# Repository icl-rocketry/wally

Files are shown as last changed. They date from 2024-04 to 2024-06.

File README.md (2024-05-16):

# Sirius

Sirius is a two stage rocket being designed and built by ICLR's Altitude Record Team (ART). This repository contains the avionics hardware and software for the rocket.

Sirius has multiple avionics systems on board, with a combination of COTS and SRAD boards used for maximum redundancy and functionality. 

COTS components used:
* [Featherweight Blue Raven](https://www.featherweightaltimeters.com/blue-raven-altimeter.html) flight computer (x2)
* [Featherweight GPS Tracker](https://www.featherweightaltimeters.com/featherweight-gps-tracker.html) (sustainer only)
* [Vodafone Curve](https://eshop.v.vodafone.com/uk/curve-gps-tracker) (booster only)

SRAD boards used:
* Pickle [(developed here)](https://github.com/icl-rocketry/Ricardo-PickleRick)
* WALLY
* Lockie
* PDU

This repository is used for the development of WALLY, Lockie, the PDU and various helper boards. 

## WALLY: Wide Area Landing Location sYstem

Wally complements the COTS trackers and the GPS system onboard Pickle to provide an independent method for trajectory reconstruction and telemetry.

It contains the following elements:
* Microcontroller - ESP32-S3
* GPS - SIM7600G
* LTE - SIM7600G
* RTC - DS3231
* 868MHz LoRa - SX1262
* Barometer - DSP368
* IMU
* Magnetometer
* Storage - Micro SD

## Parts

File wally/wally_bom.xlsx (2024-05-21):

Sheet: JLC
PCB Ident | Block | Description | Value | JLC Name | JLC Code | Basic | Cost | 0402 Code
C01 | Boost | Capacitor | 10u | CL10A106MA8NRNC | C96446 | Y | 0.0174 |  | JLC Subtotal | 0.5295
C02 | Boost | Capacitor | 10u | CL10A106MA8NRNC | C96446 | Y | 0.0174
C03 | Boost | Capacitor | 1u | CL10A105KB8NNNC | C15849 | Y | 0.0043 |  | Boards Total (USD, no VAT) | 46.13
C04 | Boost | Capacitor | 22u | CL10A226MQ8NRNC | C59461 | Y | 0.008 |  | Boards Total (GBP, VAT) | 44.2848
C05 | Boost | Capacitor | 22u | CL10A226MQ8NRNC | C59461 | Y | 0.008
C06 | Boost | Capacitor | 22u | CL10A226MQ8NRNC | C59461 | Y | 0.008 |  | Boards Ordered | 15
C07 | Boost | Capacitor | 22u | CL10A226MQ8NRNC | C59461 | Y | 0.008 |  | Unit Cost | 2.95232
C08 | Boost | Capacitor | 1u | CL10A105KB8NNNC | C15849 | Y | 0.0043
C09 | Boost | Capacitor | 100n | CC0603KRX7R9BB104 | C14663 | Y | 0.0021
C10 | LDO | Capacitor | 1u | CL10A105KB8NNNC | C15849 | Y | 0.0043
C11 | ESP | Capacitor | 100n | CC0603KRX7R9BB104 | C14663 | Y | 0.0021
C12 | ESP | Capacitor | 22u | CL10A226MQ8NRNC | C59461 | Y | 0.008
C13 | ESP | Capacitor | 100n | CC0603KRX7R9BB104 | C14663 | Y | 0.0021
C14 | USB | Capacitor | 100n | CC0603KRX7R9BB104 | C14663 | Y | 0.0021
C15 | USB | Capacitor | 1u | CL10A105KB8NNNC | C15849 | Y | 0.0043
C16 | ESP | Capacitor | 100n | CC0603KRX7R9BB104 | C14663 | Y | 0.0021
C17 | ESP | Capacitor | 100n | CC0603KRX7R9BB104 | C14663 | Y | 0.0021
C18 | ESP | Capacitor | 22u | CL10A226MQ8NRNC | C59461 | Y | 0.008
C19 | LORA | Capacitor | 100n | CC0603KRX7R9BB104 | C14663 | Y | 0.0021
C20 | Boost | Capacitor | 22u | CL10A226MQ8NRNC | C59461 | Y | 0.008
C21 | Boost | Capacitor | 22u | CL10A226MQ8NRNC | C59461 | Y | 0.008
C22 | Boost | Capacitor | 22u | CL10A226MQ8NRNC | C59461 | Y | 0.008
C23 | LORA | Capacitor | 10u | CL10A106KP8NNNC | C19702 | Y | 0.0055
C24 | IO | Capacitor | 470n | CL10B474KA8NNNC | C1623 | Y | 0.0069
C25 | IO | Capacitor | 470n | CL10B474KA8NNNC | C1623 | Y | 0.0069
C26 | IO | Capacitor | 100n | CC0603KRX7R9BB104 | C14663 | Y | 0.0021
C27 | IO | Capacitor | 100n | CC0603KRX7R9BB104 | C14663 | Y | 0.0021
C28 | IO | Capacitor | 100n | CC0603KRX7R9BB104 | C14663 | Y | 0.0021
C29 | IO | Capacitor | 100n | CC0603KRX7R9BB104 | C14663 | Y | 0.0021
C30 | Boost | Capacitor | 10u | CL10A106MA8NRNC | C96446 | Y | 0.0174
C31 | Boost | Capacitor | 10u | CL10A106MA8NRNC | C96446 | Y | 0.0174
C32 | Boost | Capacitor | 10u | CL10A106MA8NRNC | C96446 | Y | 0.0174
C33 | Boost | Capacitor | 10u | CL10A106MA8NRNC | C96446 | Y | 0.0174
C34 | Boost | Capacitor | 10u | CL10A106MA8NRNC | C96446 | Y | 0.0174
C35 | Boost | Capacitor | 100n | CC0603KRX7R9BB104 | C14663 | Y | 0.0021
C36 | Boost | Capacitor | 10u | CL10A106MA8NRNC | C96446 | Y | 0.0174
C39 | LDO | Capacitor | 22u | CL10A226MQ8NRNC | C59461 | Y | 0.008
C40 | LDO | Capacitor | 22u | CL10A226MQ8NRNC | C59461 | Y | 0.008
C41 | LDO | Capacitor | 22u | CL10A226MQ8NRNC | C59461 | Y | 0.008
C42 | LDO | Capacitor | 22u | CL10A226MQ8NRNC | C59461 | Y | 0.008
D1 | Boost | Schottky | SSA34-E3 | SS54 | C22452 | Y | 0.0422
D2 | USB | Schottky | SSA34-E3 | SS54 | C22452 | Y | 0.0422
L1 | Boost | Inductor | 10uH | SDFL1608S100KTF | C1035 | Y | 0.0097
LED1 | IO | LED | LEDG | KT-0805G | C2297 | y | 0.0132
LED2 | USB | LED | LEDW | KT-0805W | C34499 | Y | 0.0156
LED3 | USB | LED | LEDY | KT-0805Y | C2296 | Y | 0.0118
R01 | ESP | Resistor | 10k | 0603WAF1002T5E | C25804 | Y | 0.0009
R02 | Boost | Resistor | 1M | 0603WAF1004T5E | C22935 | Y | 0.0009
R03 | Boost | Resistor | 120k | 0603WAF1203T5E | C25808 | Y | 0.0009
R04 | ESP | Resistor | 1k | 0603WAF1001T5E | C21190 | Y | 0.0009
R05 | IO | Resistor | 10k | 0603WAF1002T5E | C25804 | Y | 0.0009
R06 | IO | Resistor | 10k | 0603WAF1002T5E | C25804 | Y | 0.0009
R07 | IO | Resistor | 10k | 0603WAF1002T5E | C25804 | Y | 0.0009
R08 | IO | Resistor | 10k | 0603WAF1002T5E | C25804 | Y | 0.0009
R09 | ESP | Resistor | 100k | 0603WAF1003T5E | C25803 | Y | 0.0009
R10 | ESP | Resistor | 20k | 0603WAF2002T5E | C4184 | Y | 0.0009
R11 | ESP | Resistor | 1k | 0603WAF1001T5E | C21190 | Y | 0.0009
R12 | USB | Resistor | 5k1 | 0603WAF5101T5E | C23186 | Y | 0.0009
R13 | USB | Resistor | 1M | 0603WAF1004T5E | C22935 | Y | 0.0009
R14 | USB | Resistor | 5k1 | 0603WAF5101T5E | C23186 | Y | 0.0009
R15 | IO | Resistor | 33 | 0603WAF330JT5E | C23140 | Y | 0.0009
R16 | ESP | Resistor | 100 | 0603WAF1000T5E | C22775 | Y | 0.001
R17 | IO | Resistor | 150 | 0603WAF1500T5E | C22808 | Y | 0.0009
LED4 | IO | LED | LEDG | KT-0805G | C2297 | y | 0.0132
LED5 | IO | LED | LEDG | KT-0805G | C2297 | y | 0.0132
LED6 | IO | LED | LEDR | NCD0805R1 | C84256 | y | 0.0126
R18 | IO | Resistor | 33 | 0603WAF330JT5E | C23140 | Y | 0.0009
R19 | IO | Resistor | 33 | 0603WAF330JT5E | C23140 | Y | 0.0009
R20 | IO | Resistor | 51 | 0603WAF510JT5E | C23197 | Y | 0.0009
S1 | IO | Switch |  | TS-1187A-B-A-B | C318884 | Y | 0.0164
S2 | IO | Switch |  | TS-1187A-B-A-B | C318884 | Y | 0.0164

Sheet: Flight Version
PCB Ident | Desc | Name | Link | Supplier | Unit Cost | Quantity Required | Subtotal | Optional | added to order
U1 | LoRa Module | AI Thinker RA-01SH | https://www.aliexpress.com/item/1005002561194884.html | Aliexpress | 3.535555556 | 1 | 3.535555556 | n | y | Mandatory Components | 21.22555556
IC1 | MCU | ESP32-S3-WROOM-1-N16R2 | https://www.mouser.co.uk/ProductDetail/Espressif-Systems/ESP32-S3-WROOM-1-N16R2 | Mouser | 2.9 | 1 | 2.9 | n | y | Optional Components | 40.95
IC2 | Boost | TI TLV61048DBVR | https://www.mouser.co.uk/ProductDetail/Texas-Instruments/TLV61048DBVR?qs=vLWxofP3U2yo%2F8t1L3OASw%3D%3D | Mouser | 0.56 | 1 | 0.56 | n | y | Board manufacture cost | 2.95232
IC3 | LDO | TLV1117LV33DCYR | https://www.mouser.co.uk/ProductDetail/Texas-Instruments/TLV1117LV33DCYR?qs=tEz3BkPb1rwzXMb8FiWhow%3D%3D | Mouser | 0.28 | 1 | 0.28 | n | y
J1 | Micro SD | MSD-4-A | https://www.mouser.co.uk/ProductDetail/CUI-Devices/MSD-4-A?qs=Z%252BL2brAPG1Jll%252BQTi%252Btupg%3D%3D | Mouser | 0.28 | 1 | 0.28 | n | y | Per Board Total | 65.12787556
USB | USB C Port | USB4105-GF-A-120 | https://www.mouser.co.uk/ProductDetail/GCT/USB4105-GF-A-120?qs=QNEnbhJQKva%252Bjxw%2FpEjDhQ%3D%3D | Mouser | 0.66 | 1 | 0.66 | n | y | Boards Required | 1
SIM | LTE Module | SIM 7600G | https://www.aliexpress.com/item/4000449295553.html | Aliexpress | 29.33 | 1 | 29.33 | y | y
IC4 | Barometer | DPS368XTSA1 | https://www.mouser.co.uk/ProductDetail/Infineon-Technologies/DPS368XTSA1?qs=l7cgNqFNU1issZx9oeCNag%3D%3D | Mouser | 2.49 | 1 | 2.49 | n | y | Total | 65.12787556
IC9 | Env sensor | BME680 | https://www.mouser.co.uk/ProductDetail/Bosch-Sensortec/BME680?qs=v271MhAjFHjo0yA%2FC4OnDQ%3D%3D | Mouser | 8.61 | 1 |  | y | y
IC8 | Light sensor | APSD-9523 | https://www.mouser.co.uk/ProductDetail/Broadcom-Avago/APDS-9253-001?qs=T3oQrply3y9os9rwnJ1p%252Bg%3D%3D | Mouser | 1.97 | 2 |  | y | y
IC7 | Mag | MMC5983 | https://www.mouser.co.uk/ProductDetail/MEMSIC/MMC5983MA?qs=B6kkDfuK7%2FD5qasHMdEt2g%3D%3D | Mouser | 2.88 | 2 |  | n | y
RTC | RTC | DS3231 | https://www.aliexpress.com/item/1005006254225186.html | Aliexpress | 0.87 | 1 | 0.87 | y | y
IC6 | IMU | LSM6DSV32 | https://www.mouser.co.uk/ProductDetail/STMicroelectronics/LSM6DSV32XTR?qs=HoCaDK9Nz5d%252BGVBpjxkjlg%3D%3D | Mouser | 5.26 | 2 | 10.52 | n | y
AC1 | Accelerometer | H3LIS331 | https://www.mouser.co.uk/ProductDetail/STMicroelectronics/H3LIS331DLTR?qs=TAo1I7FhABsAZFqkqNUSRA%3D%3D | Mouser | 10.75 | 1 | 10.75 | y | y

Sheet: Ground Version
PCB Ident | Desc | Name | Link | Supplier | Unit Cost | Quantity Required | Subtotal | Optional
U1 | LoRa Module | AI Thinker RA-01SH | https://www.aliexpress.com/item/1005002561194884.html | Aliexpress | 3.535555556 | 1 | 3.535555556 | n | Mandatory Components | 10.12555556
IC1 | MCU | ESP32-S3-WROOM-1-N16R2 | https://www.mouser.co.uk/ProductDetail/Espressif-Systems/ESP32-S3-WROOM-1-N16R2 | Mouser | 2.9 | 1 | 2.9 | n | Optional Components | 0.87
IC2 | Boost | TI TLV61048DBVR | https://www.mouser.co.uk/ProductDetail/Texas-Instruments/TLV61048DBVR?qs=vLWxofP3U2yo%2F8t1L3OASw%3D%3D | Mouser | 0.56 | 1 | 0.56 | n | Board manufacture cost | 2.95232
IC3 | LDO | TLV1117LV33DCYR | https://www.mouser.co.uk/ProductDetail/Texas-Instruments/TLV1117LV33DCYR?qs=tEz3BkPb1rwzXMb8FiWhow%3D%3D | Mouser | 0.28 | 1 | 0.28 | n
J1 | Micro SD | MSD-4-A | https://www.mouser.co.uk/ProductDetail/CUI-Devices/MSD-4-A?qs=Z%252BL2brAPG1Jll%252BQTi%252Btupg%3D%3D | Mouser | 0.28 | 1 | 0.28 | n | Per Board Total | 13.94787556
USB | USB C Port | 217175-0001 | https://www.mouser.co.uk/ProductDetail/Molex/217175-0001?qs=DRkmTr78QARWJMiqNnldSg%3D%3D | Mouser | 0.65 | 1 | 0.65 | n | Boards Required | 6
GPS | GPS Module | NEO-7M | https://www.aliexpress.com/item/1005005475472834.html | Aliexpress | 1.92 | 1 | 1.92 | n
RTC | RTC | DS3231 | https://www.aliexpress.com/item/1005006254225186.html | Aliexpress | 0.87 | 1 | 0.87 | y | Total | 101.4011733

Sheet: JLC_Extended
PCB Ident | Block | Description | Value | JLC Name | JLC Code | Unit Cost | Total Cost
J5 | USB | USB C Connector |  | MC-107DB | C3039324 | 0.1683 | 5.5245 | Part Subtotal | 91.119
IC2 | Power | Boost converter |  | TLV61048DBVR | C2861467 | 0.204 | 6.06
IC5 | Sensors | IMU |  | BMI323 | C5368700 | 1.4025 | 24.0375
IC4 | Sensors | Baro |  | DPS368 | C3232508 | 3.1455 | 50.1825
IC3 | Power | LDO |  | TLV1117LV33DCYR | C15578 | 0.1543 | 5.3145
 |  |  |  |  |  |  |  | Boards Ordered | 15
 |  |  |  |  |  |  |  | Unit Cost | 6.0746

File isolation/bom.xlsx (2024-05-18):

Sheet: JLC
PCB Ident | Block | Description | Simple Name | JLC Name | JLC Code | Basic | Cost
D1 | Power | Schottky | Schottky Diode 5A | SS54 | C22452 | Y | 0.0422 | JLC Subtotal | 0.4518
C02 | Power | Boost end cap | 20V 10u cap | CL10A106MA8NRNC | C96446 | Y | 0.0174
C16 | Output | Bulk Cap | 20V 10u cap | CL10A106MA8NRNC | C96446 | Y | 0.0174 | Boards Total (USD, no VAT) | 37.27
C17 | Output | Bulk Cap | 20V 10u cap | CL10A106MA8NRNC | C96446 | Y | 0.0174 | Boards Total (GBP, VAT) | 35.7792
C18 | Output | Bulk Cap | 20V 10u cap | CL10A106MA8NRNC | C96446 | Y | 0.0174
C19 | Output | Bulk Cap | 20V 10u cap | CL10A106MA8NRNC | C96446 | Y | 0.0174 | Boards Ordered | 10
LED01 | Battery | Pow LED | White LED | KT-0805W | C34499 | Y | 0.0156 | Unit Cost | 3.57792
LED03 | Lock | Disabled LED | Green LED | KT-0805G | C2297 | y | 0.0132
LED05 | Lock | Disabled LED | Green LED | KT-0805G | C2297 | y | 0.0132
LED06 | Indicator | Show firing channel | Red LED | NCD0805R1 | C84256 | Y | 0.0126
LED07 | Indicator | Show firing channel | Red LED | NCD0805R1 | C84256 | Y | 0.0126
LED08 | Indicator | Show firing channel | Red LED | NCD0805R1 | C84256 | Y | 0.0126
LED09 | Indicator | Show firing channel | Red LED | NCD0805R1 | C84256 | Y | 0.0126
LED10 | Indicator | Show firing channel | Red LED | NCD0805R1 | C84256 | Y | 0.0126
LED11 | Indicator | Show firing channel | Red LED | NCD0805R1 | C84256 | Y | 0.0126
LED12 | Indicator | Show firing channel | Red LED | NCD0805R1 | C84256 | Y | 0.0126
LED13 | Indicator | Show firing channel | Red LED | NCD0805R1 | C84256 | Y | 0.0126
LED14 | Indicator | Show firing channel | Red LED | NCD0805R1 | C84256 | Y | 0.0126
LED02 | Lock | Enable LED | Yellow LED | KT-0805Y | C2296 | Y | 0.0118
LED04 | Lock | Enable LED | Yellow LED | KT-0805Y | C2296 | Y | 0.0118
L1 | Power | Inductor | 10uH inductor | SDFL1608S100KTF | C1035 | Y | 0.0097
C04 | Power | Input Cap | 22u cap | CL10A226MQ8NRNC | C59461 | Y | 0.008
C05 | Power | Input Cap | 22u cap | CL10A226MQ8NRNC | C59461 | Y | 0.008
C06 | Power | Input Cap | 22u cap | CL10A226MQ8NRNC | C59461 | Y | 0.008
C07 | Power | Input Cap | 22u cap | CL10A226MQ8NRNC | C59461 | Y | 0.008
C20 | Power | Bulk Cap | 22u cap | CL10A226MQ8NRNC | C59461 | Y | 0.008
C21 | Power | Bulk Cap | 22u cap | CL10A226MQ8NRNC | C59461 | Y | 0.008
C22 | Power | Bulk Cap | 22u cap | CL10A226MQ8NRNC | C59461 | Y | 0.008
D2 | USB | Drop Diode | Diode | SM4007PL | C64898 | Y | 0.0068
D3 | USB | Drop Diode | Diode | SM4007PL | C64898 | Y | 0.0068
D4 | USB | Drop Diode | Diode | SM4007PL | C64898 | Y | 0.0068
C01 | Power | Input Cap | 10V 10u cap | CL10A106KP8NNNC | C19702 | Y | 0.0055
C03 | Power | Rectifier Cap | 1u cap | CL10A105KB8NNNC | C15849 | Y | 0.0043
C09 | Logic | Inverter Cap | 1u cap | CL10A105KB8NNNC | C15849 | Y | 0.0043
C11 | Logic | Inverter Cap | 1u cap | CL10A105KB8NNNC | C15849 | Y | 0.0043
C13 | Logic | Inverter Cap | 1u cap | CL10A105KB8NNNC | C15849 | Y | 0.0043
C15 | USB | Filter Cap | 1u cap | CL10A105KB8NNNC | C15849 | Y | 0.0043
C08 | Logic | Inverter Cap | 100n cap | CC0603KRX7R9BB104 | C14663 | Y | 0.0021
C10 | Logic | Inverter Cap | 100n cap | CC0603KRX7R9BB104 | C14663 | Y | 0.0021
C12 | Logic | Inverter Cap | 100n cap | CC0603KRX7R9BB104 | C14663 | Y | 0.0021
C14 | USB | Filter Cap | 100n cap | CC0603KRX7R9BB104 | C14663 | Y | 0.0021
R01 | Battery | Pow LED R | R 75 | 0603WAF750JT5E | C4275 | Y | 0.001
R04 | Lock | Enable LED R | R 120 | 0603WAF1200T5E | C22787 | Y | 0.001
R05 | Lock | Enable LED R | R 120 | 0603WAF1200T5E | C22787 | Y | 0.001
R06 | Lock | Disabled LED R | R 100 | 0603WAF1000T5E | C22775 | Y | 0.001
R07 | Lock | Disabled LED R | R 100 | 0603WAF1000T5E | C22775 | Y | 0.001
R15 | Indicator | LED R | R 120 | 0603WAF1200T5E | C22787 | Y | 0.001
R16 | Indicator | LED R | R 120 | 0603WAF1200T5E | C22787 | Y | 0.001
R17 | Indicator | LED R | R 120 | 0603WAF1200T5E | C22787 | Y | 0.001
R18 | Indicator | LED R | R 120 | 0603WAF1200T5E | C22787 | Y | 0.001
R19 | Indicator | LED R | R 120 | 0603WAF1200T5E | C22787 | Y | 0.001
R20 | Indicator | LED R | R 120 | 0603WAF1200T5E | C22787 | Y | 0.001
R21 | Indicator | LED R | R 120 | 0603WAF1200T5E | C22787 | Y | 0.001
R22 | Indicator | LED R | R 120 | 0603WAF1200T5E | C22787 | Y | 0.001
R23 | Indicator | LED R | R 120 | 0603WAF1200T5E | C22787 | Y | 0.001
R02 | Power | V Div R1 | R 1M | 0603WAF1004T5E | C22935 | Y | 0.0009
R03 | Power | V Div R2 | R 68k | 0603WAF6802T5E | C23231 | Y | 0.0009
R08 | Relay | Pulldown R | R 68k | 0603WAF6802T5E | C23231 | Y | 0.0009
R09 | Relay | Pulldown R | R 68k | 0603WAF6802T5E | C23231 | Y | 0.0009
R10 | Relay | Pulldown R | R 68k | 0603WAF6802T5E | C23231 | Y | 0.0009
R11 | Relay | Pulldown R | R 68k | 0603WAF6802T5E | C23231 | Y | 0.0009
R12 | USB | Pulldown R | R 5k1 | 0603WAF5101T5E | C23186 | Y | 0.0009
R13 | USB | Protection R | R 1M | 0603WAF1004T5E | C22935 | Y | 0.0009
R14 | USB | Pulldown R | R 5k1 | 0603WAF5101T5E | C23186 | Y | 0.0009

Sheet: Other
PCB Ident | Desc | Name | Link | Supplier | Unit Cost | Added to order
 | Buzzer | CMI-9705-85-SMT-TR | https://www.mouser.co.uk/ProductDetail/CUI-Devices/CMI-9705-85-SMT-TR?qs=P1JMDcb91o4Wun0lW9vptg%3D%3D | Mouser | 1.2 | y | Components Total | 6.346
E1 | Input | SJ1-3525N | https://www.mouser.co.uk/ProductDetail/CUI-Devices/SJ1-3525N?qs=WyjlAZoYn505QPmBO3I74g%3D%3D | Mouser | 0.88 | y | Boards Cost | 3.57792
E2 | Input | SJ1-3525N | https://www.mouser.co.uk/ProductDetail/CUI-Devices/SJ1-3525N?qs=WyjlAZoYn505QPmBO3I74g%3D%3D | Mouser | 0.88 | y
USB | USB C Port | UJC-HP2-3-SMT-TR | https://www.mouser.co.uk/ProductDetail/CUI-Devices/UJC-HP2-3-SMT-TR?qs=HoCaDK9Nz5cglCCyoWNzZg%3D%3D | Mouser | 0.464 | y
IC1 | Boost | TI TLV61048DBVR | https://www.mouser.co.uk/ProductDetail/Texas-Instruments/TLV61048DBVR?qs=vLWxofP3U2yo%2F8t1L3OASw%3D%3D | Mouser | 0.552 | y | Board Subtotal | 9.92392
IC5 | MOSFET | FDN359BN | https://www.mouser.co.uk/ProductDetail/onsemi-Fairchild/FDN359BN?qs=8YYpzd7qSxKZfze3Gm99uA%3D%3D | Mouser | 0.37 | y | Boards Required | 6
IC6 | MOSFET | FDN359BN | https://www.mouser.co.uk/ProductDetail/onsemi-Fairchild/FDN359BN?qs=8YYpzd7qSxKZfze3Gm99uA%3D%3D | Mouser | 0.37 | y | Total Cost | 59.54352
IC7 | MOSFET | FDN359BN | https://www.mouser.co.uk/ProductDetail/onsemi-Fairchild/FDN359BN?qs=8YYpzd7qSxKZfze3Gm99uA%3D%3D | Mouser | 0.37 | y
IC8 | MOSFET | FDN359BN | https://www.mouser.co.uk/ProductDetail/onsemi-Fairchild/FDN359BN?qs=8YYpzd7qSxKZfze3Gm99uA%3D%3D | Mouser | 0.37 | y
IC3 | OR gate | SN74HCS32BQAR | https://www.mouser.co.uk/ProductDetail/Texas-Instruments/SN74HCS32BQAR?qs=stqOd1AaK78oD0q8sZ5E5Q%3D%3D | Mouser | 0.32 | y
IC2 | Inverter | SN74HC14PWR | https://www.mouser.co.uk/ProductDetail/Texas-Instruments/SN74HC14PWR?qs=YEaxc5757jODQ8PDizZzPA%3D%3D | Mouser | 0.31 | y
IC4 | AND gate | SN74HCS08DYYR | https://www.mouser.co.uk/ProductDetail/Texas-Instruments/SN74HCS08DYYR?qs=Li%252BoUPsLEnuxOc6m1Nu7zQ%3D%3D | Mouser | 0.26 | y
J1 | Input | JST-PH 4 pin
J2 | Input | JST-PH 4 pin
J3 | Output | JST-PH 2 pin
J4 | Output | JST-PH 2 pin
J5 | Output | JST-PH 2 pin
BAT1 | Power | JST-PH 2 pin
BAT2 | Power | JST-PH 2 pin

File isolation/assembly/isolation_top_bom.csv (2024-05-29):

Comment | Designator | Footprint | LCSC Part #
1M | R2 R13 | RESC1005X40 | C26083
1u | C3 C9 C11 C13 C15 C25 | CAPC1005X60 | C52923
5k1 | R12 R14 | RESC1005X40 | C25905
10u | C1 | CAPC1005X60 | C15525
10u | C2 C16 C17 C18 C19 C23 | CAPC1608X85 | C96446
10μH | L1 | BMRF00060630100MA1 | C305184
22u | C4 C5 C6 C7 C20 C21 C22 | CAPC1608X85 | C59461
47k | R6 R7 R8 R9 R10 R11 R28 R29 R30 R31 | RESC1005X40 | C25792
68k | R3 | RESC1608X60 | C23231
75 | R1 | RESC1608X60 | C4275
100n | C8 C10 C12 C14 C24 | CAPC1005X60 | C1525
120 | R4 R5 R15 R16 R17 R18 R19 R20 R21 R22 R23 | RESC1005X40 | C25079
470 | R24 R25 R26 R27 | RESC1005X40 | C25117
10164359-00011LF | J7 | 1016435900011LF
CMI-9705-85-SMT-TR | LS1 | CMI970585SMTTR
FDN359BN | IC5 IC6 IC7 IC8 | SOT95P251X112-3N | C5290365
LEDR | LED6 LED7 LED8 LED9 LED10 LED11 LED12 LED13 LED14 | CHIPLED_0805 | C84256
LEDW | LED1 | CHIPLED_0805 | C34499
LEDY | LED2 LED4 | CHIPLED_0805 | C2296
SN74HC14PWR | IC2 IC9 | SOP65P640X120-14N | C6821
SN74HCS08BQAR | IC4 | SN74HCS08BQAR | C4470281
SN74HCS32BQAR | IC3 | SN74HCS32BQAR | C4471379
SSA34-E3_5AT | D1 | DIOM5127X229N | C22452
USBDiode | D2 | SOD-123FL | C64898
XTLV61048DBVR | IC1 | SOT95P280X145-6N | C2861467

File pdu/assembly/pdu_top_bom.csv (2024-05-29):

Comment | Designator | Footprint | LCSC Part #
1u | C5 C8 C11 C14 C17 C20 C23 C26 C29 C32 | CAPC1608X85 | C15849
22u | C6 C9 C12 C15 C18 C21 C24 C27 C30 C33 | CAPC1608X85 | C59461
68k | R2 | RESC1608X60 | C23231
100 | R6 | RESC1608X60 | C22775
100n | C4 C7 C10 C13 C16 C19 C22 C25 C28 C31 | CAPC1608X85 | C14663
120 | R4 | RESC1608X60 | C22787
470 | R1 | RESC1608X60 | C23179
LEDG | LED3 | CHIPLED_0805 | C2297
LEDY | LED2 | CHIPLED_0805 | C2296
TSM4806CS_RLG | Q1 | SOP127P600X200-8N

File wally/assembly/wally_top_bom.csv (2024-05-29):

Comment | Designator | Footprint | LCSC Part #
1M | R2 | RESC1608X60 | C22935
1M | R13 | RESC1005X40 | C26083
1k | R4 R11 | RESC1005X40 | C11702
1u | C3 C8 C10 C15 C44 C46 | CAPC1005X60 | C52923
5k1 | R5 R6 R7 R8 | RESC1005X40 | C25905
5k1 | R12 R14 | RESC1608X60 | C23186
10k | R1 | RESC1005X40 | C25744
10u | C1 | CAPC1005X60 | C15525
10u | C2 | CAPC1608X85 | C96446
10u | C23 C24 | CAPC1005X60 | C15525
10u | C30 C31 C32 C33 C34 C36 | CAPC1608X85 | C96446
10uH | L1 | BMRF00060630100MA1
20k | R10 | RESC1005X40 | C25765
22u | C4 C5 C6 C7 C12 C18 C20 C21 C22 C39 C40 C41 C42 | CAPC1608X85 | C59461
33 | R15 R18 | RESC1005X40 | C25105
51 | R20 | RESC1608X60 | C23197
75 | R19 | RESC1608X60 | C4275
100 | R16 | RESC1005X40 | C25076
100k | R9 | RESC1005X40 | C25741
100n | C9 C11 C13 C14 C16 C17 C19 C25 C26 C27 C28 C29 C35 C37 C38 C43 C45 | CAPC1005X60 | C1525
120k | R3 | RESC1608X60 | C25808
150 | R17 | RESC1608X60 | C22808
APDS-9253-001 | IC8 | APDS9253001
BME688 | IC9 | BME688
DPS368XTSA1 | IC4 | DPS368XTSA1
ESP32-S3-WROOM-1U-N16 | IC1 | ESP32S3WROOM1UN16
H3LIS331DLTR | AC1 | LIS3DHTR
JUMPER-SMT_2_NO_SILK | JP4 JP5 | SMT-JUMPER_2_NO_SILK
LEDG | LED1 LED4 | CHIPLED_0805 | C2297
LEDR | LED6 | CHIPLED_0805 | C84256
LEDW | LED2 | CHIPLED_0805 | C34499
LEDY | LED3 LED5 | CHIPLED_0805 | C2296
LSM6DSV16BXTR | IC6 | LSM6DSV16BXTR
MMC5983MA | IC7 | MMC5983MA
MSD-4-A | J1 | MSD4A
QWIIC_RIGHT_ANGLE | J2 J3 | JST04_1MM_RA
RA-01H | U1 | XCVR_RA-01H
SSA34-E3_5AT | D1 D2 | DIOM5127X229N | C22452
TLV1117LV33DCYR | IC3 | SOT230P700X180-4N | C15578
TS-1187A-B-A-B | S1 S2 | TS1187ABAB | C318884
USB4105-GF-A | J5 | GCT_USB4105-GF-A | C3039324
XTLV61048DBVR | IC2 | SOT95P280X145-6N | C2861467

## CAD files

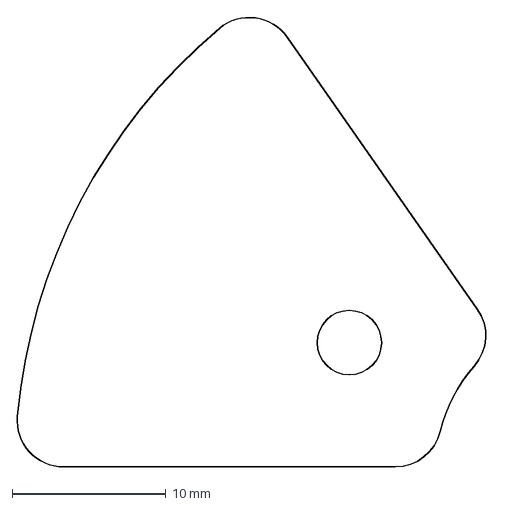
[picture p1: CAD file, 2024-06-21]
helpers/sustainer_ps.dxf
30.8 x 29.3 mm

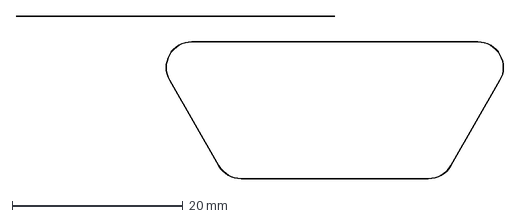
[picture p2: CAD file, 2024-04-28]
isolation/cutout.dxf
57.1 x 19.0 mm

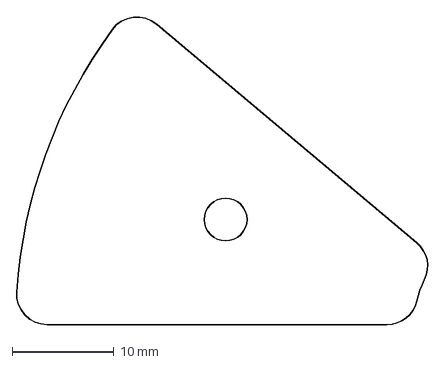
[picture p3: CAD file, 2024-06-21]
helpers/booster_ps.dxf
40.7 x 30.3 mm

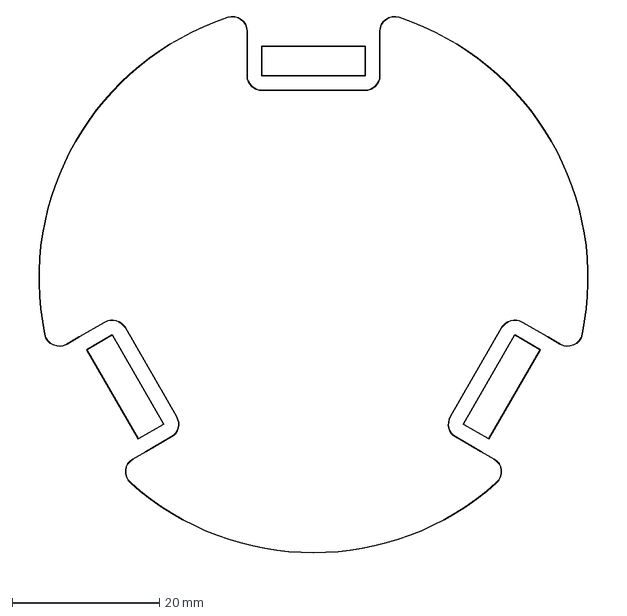
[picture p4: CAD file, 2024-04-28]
isolation/outline.dxf
80.7 x 76.0 mm

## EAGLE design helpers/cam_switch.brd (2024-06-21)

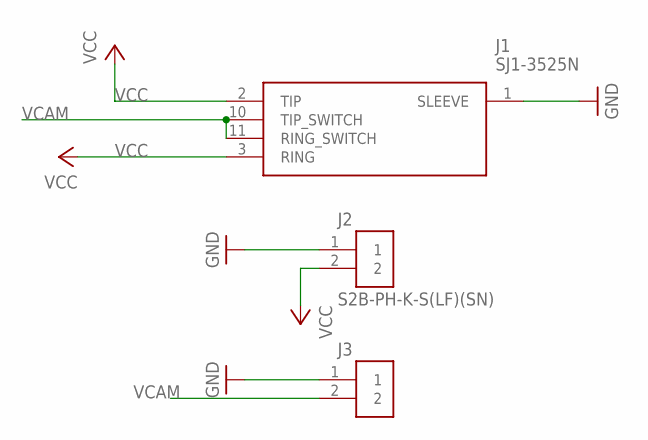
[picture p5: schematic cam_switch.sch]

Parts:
J1: SJ1-3525N; SJ13525N
J2, J3: S2B-PH-K-S(LF)(SN)

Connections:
GND: J1.1 (SLEEVE), J2.1, J3.1
VCAM: J1.10 (TIP_SWITCH), J1.11 (RING_SWITCH), J3.2
VCC: J1.2 (TIP), J1.3 (RING), J2.2

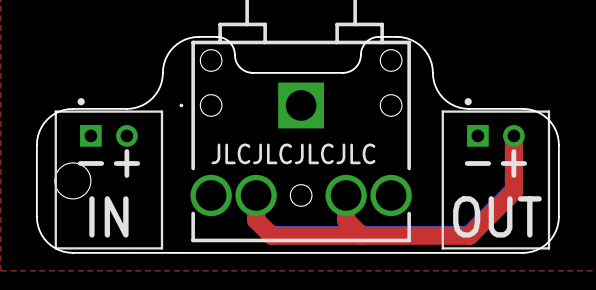
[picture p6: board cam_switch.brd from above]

Board: 2 copper layers, 29.0 x 12.0 mm, 3 parts (0 on the bottom side), 3 nets.

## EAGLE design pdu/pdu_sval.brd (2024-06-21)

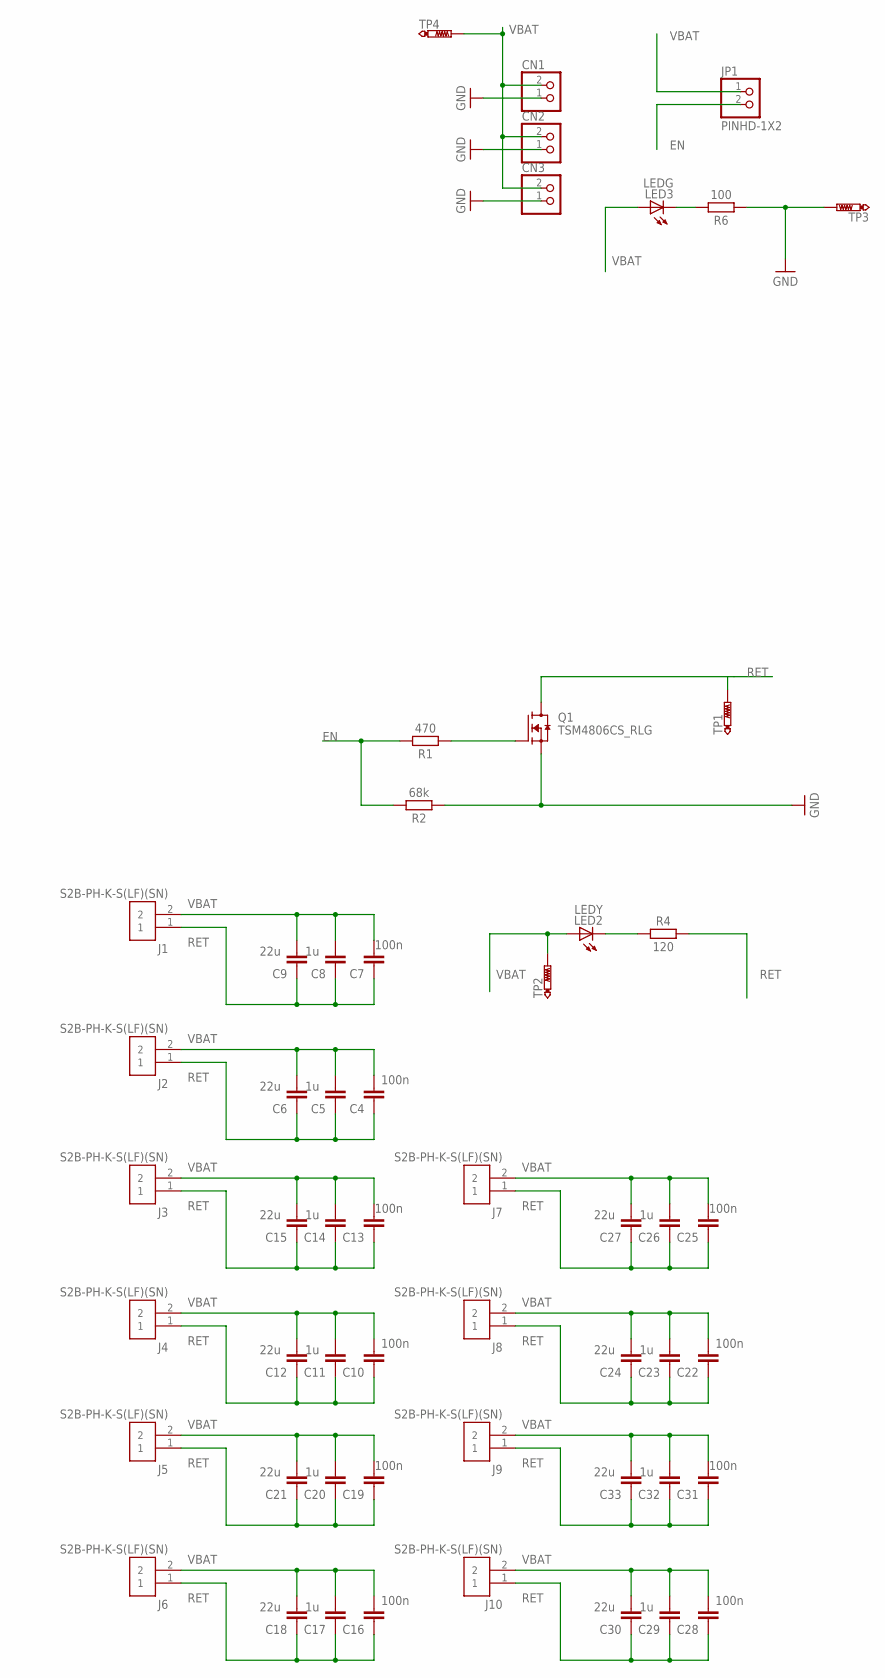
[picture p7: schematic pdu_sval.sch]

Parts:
C4, C7, C10, C13, C16, C19, C22, C25, C28, C31: 100n; CAPC1608X85
C5, C8, C11, C14, C17, C20, C23, C26, C29, C32: 1u; CAPC1608X85
C6, C9, C12, C15, C18, C21, C24, C27, C30, C33: 22u; CAPC1608X85
CN1, CN2, CN3: JST_2PIN-THM-RA; JST-PH-2-THM-RA
J1, J2, J3, J4, J5, J6, J7, J8, J9, J10: S2B-PH-K-S(LF)(SN)
JP1: PINHD-1X2; 1X02
LED2: LEDY; CHIPLED_0805
LED3: LEDG; CHIPLED_0805
Q1: TSM4806CS_RLG; SOP127P600X200-8N
R1: 470; RESC1608X60
R2: 68k; RESC1608X60
R4: 120; RESC1608X60
R6: 100; RESC1608X60
TP1, TP2, TP3, TP4: PTR1PAD1-13; P1-13

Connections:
EN: JP1.2, R1.2, R2.2
GND: CN1.1 (2), CN2.1 (2), CN3.1 (2), Q1.1 (S), Q1.2 (S), Q1.3 (S), R2.1, R6.1, TP3.TP
unnamed: Q1.4 (G), R1.1
unnamed: LED3.C, R6.2
unnamed: LED2.C, R4.1
RET: C4.1, C5.1, C6.1, C7.1, C8.1, C9.1, C10.1, C11.1, C12.1, C13.1, C14.1, C15.1, C16.1, C17.1, C18.1, C19.1, C20.1, C21.1, C22.1, C23.1, C24.1, C25.1, C26.1, C27.1, C28.1, C29.1, C30.1, C31.1, C32.1, C33.1, J1.1, J2.1, J3.1, J4.1, J5.1, J6.1, J7.1, J8.1, J9.1, J10.1, Q1.5 (D), Q1.6 (D), Q1.7 (D), Q1.8 (D), R4.2, TP1.TP
VBAT: C4.2, C5.2, C6.2, C7.2, C8.2, C9.2, C10.2, C11.2, C12.2, C13.2, C14.2, C15.2, C16.2, C17.2, C18.2, C19.2, C20.2, C21.2, C22.2, C23.2, C24.2, C25.2, C26.2, C27.2, C28.2, C29.2, C30.2, C31.2, C32.2, C33.2, CN1.2 (1), CN2.2 (1), CN3.2 (1), J1.2, J2.2, J3.2, J4.2, J5.2, J6.2, J7.2, J8.2, J9.2, J10.2, JP1.1, LED2.A, LED3.A, TP2.TP, TP4.TP

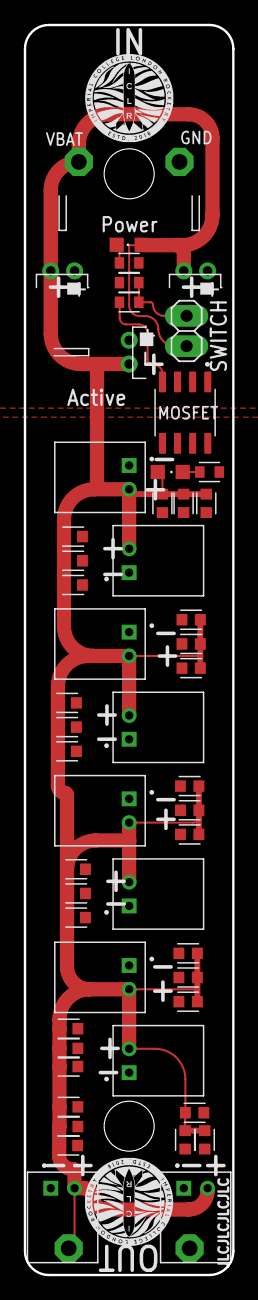
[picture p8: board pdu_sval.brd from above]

Board: 2 copper layers, 17.5 x 105.0 mm, 55 parts (0 on the bottom side), 7 nets.

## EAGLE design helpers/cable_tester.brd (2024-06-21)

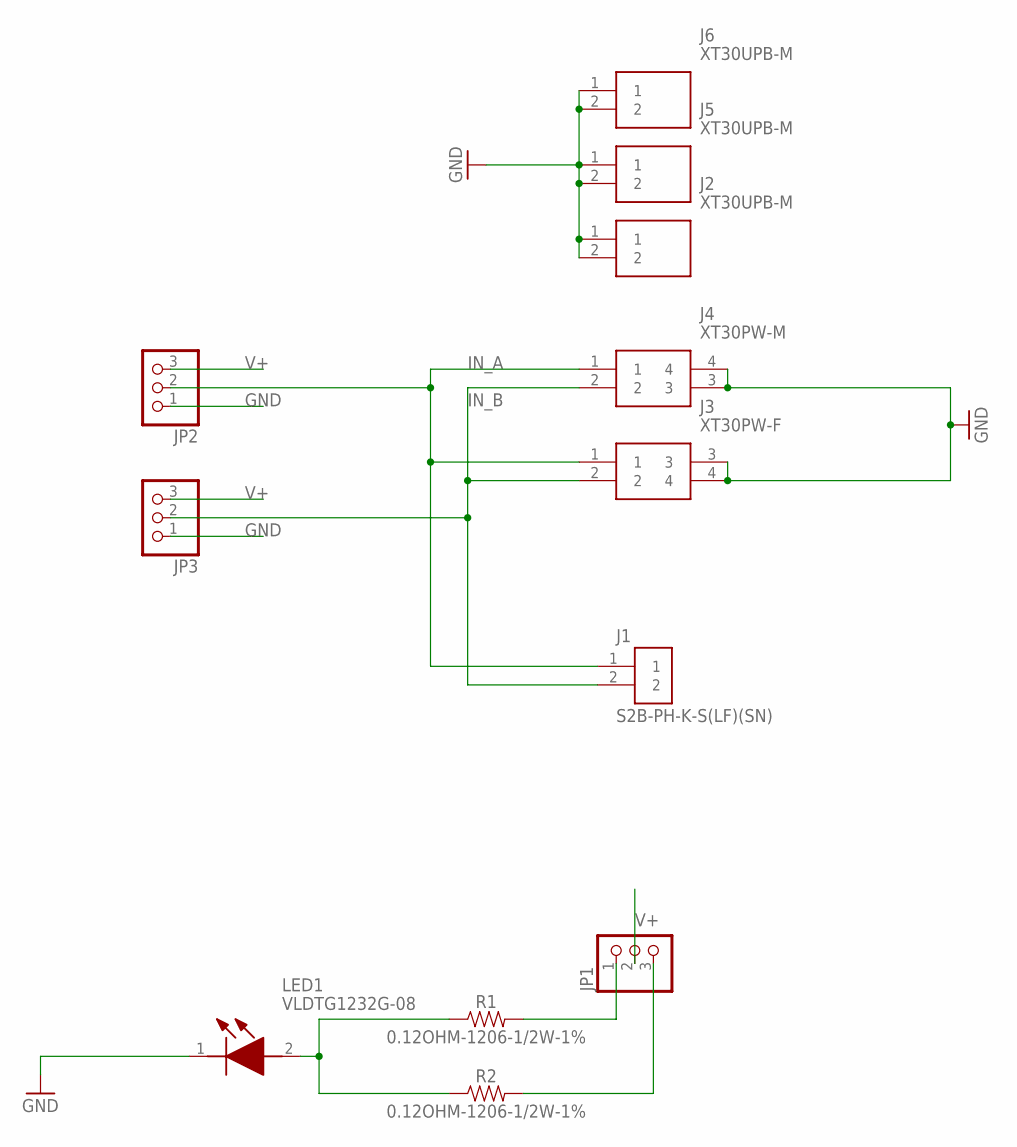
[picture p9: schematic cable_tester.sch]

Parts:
J1: S2B-PH-K-S(LF)(SN)
J2, J5, J6: XT30UPB-M; SHDR2W160P0X500_1X2_1020X520X1
J3: XT30PW-F; XT30PWF
J4: XT30PW-M; XT30PWM
JP1, JP2, JP3: PINHD-1X3; 1X03
LED1: VLDTG1232G-08; VLDTG1232G08
R1, R2: 0.12OHM-1206-1/2W-1%; 1206

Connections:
GND: J2.1, J2.2, J3.3, J3.4, J4.3, J4.4, J5.1, J5.2, J6.1, J6.2, JP2.1, JP3.1, LED1.1 (K)
IN_A: J1.1, J3.1, J4.1, JP2.2
IN_B: J1.2, J3.2, J4.2, JP3.2
unnamed: LED1.2 (A), R1.1, R2.1
unnamed: JP1.1, R1.2
unnamed: JP1.3, R2.2
V+: JP1.2, JP2.3, JP3.3

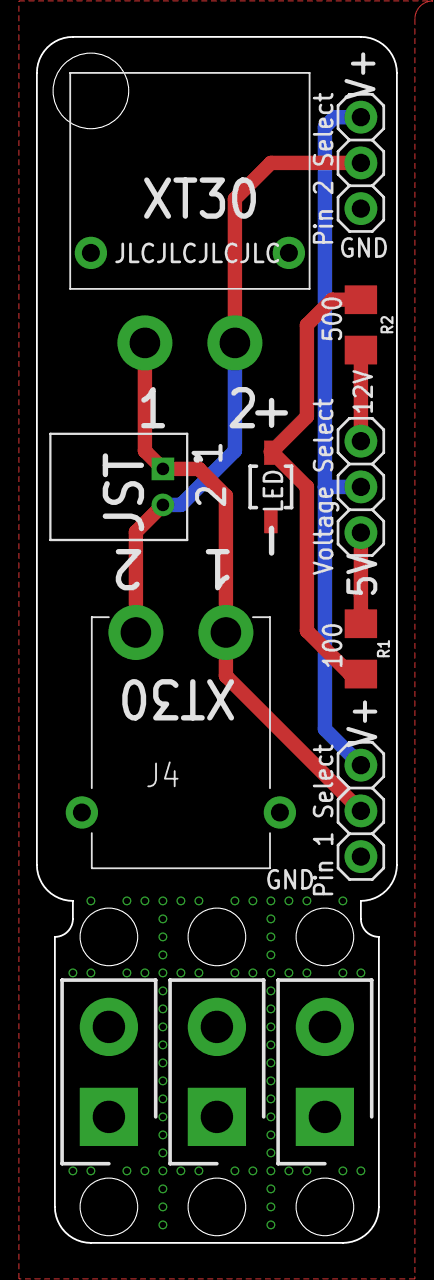
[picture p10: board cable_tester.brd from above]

Board: 2 copper layers, 20.0 x 67.0 mm, 12 parts (0 on the bottom side), 7 nets.

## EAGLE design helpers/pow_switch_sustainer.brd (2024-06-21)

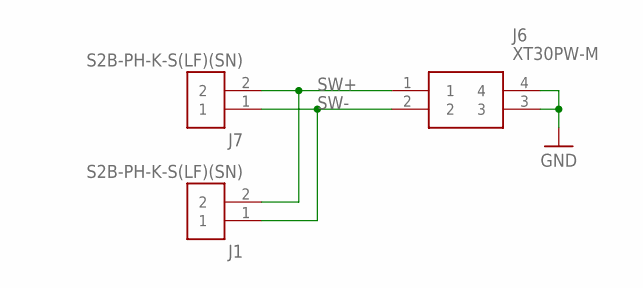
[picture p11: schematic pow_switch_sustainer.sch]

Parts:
J1, J7: S2B-PH-K-S(LF)(SN)
J6: XT30PW-M; XT30PWM

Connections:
GND: J6.3, J6.4
SW+: J1.2, J6.1, J7.2
SW-: J1.1, J6.2, J7.1

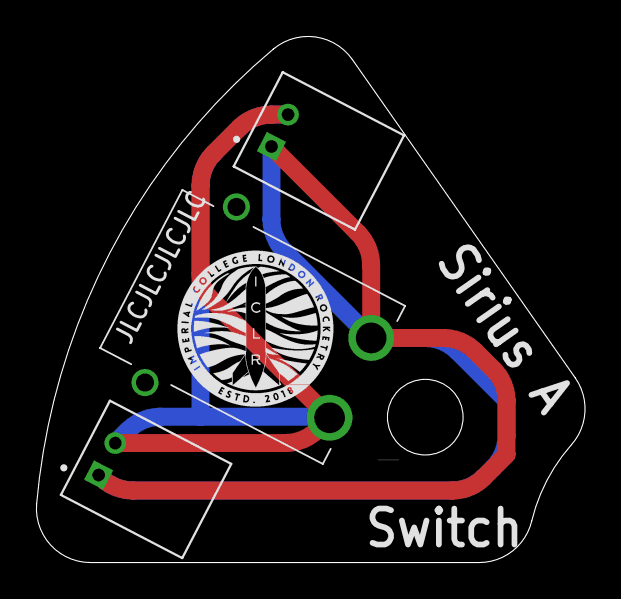
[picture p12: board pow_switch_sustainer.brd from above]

Board: 2 copper layers, 30.5 x 29.2 mm, 3 parts (0 on the bottom side), 3 nets.

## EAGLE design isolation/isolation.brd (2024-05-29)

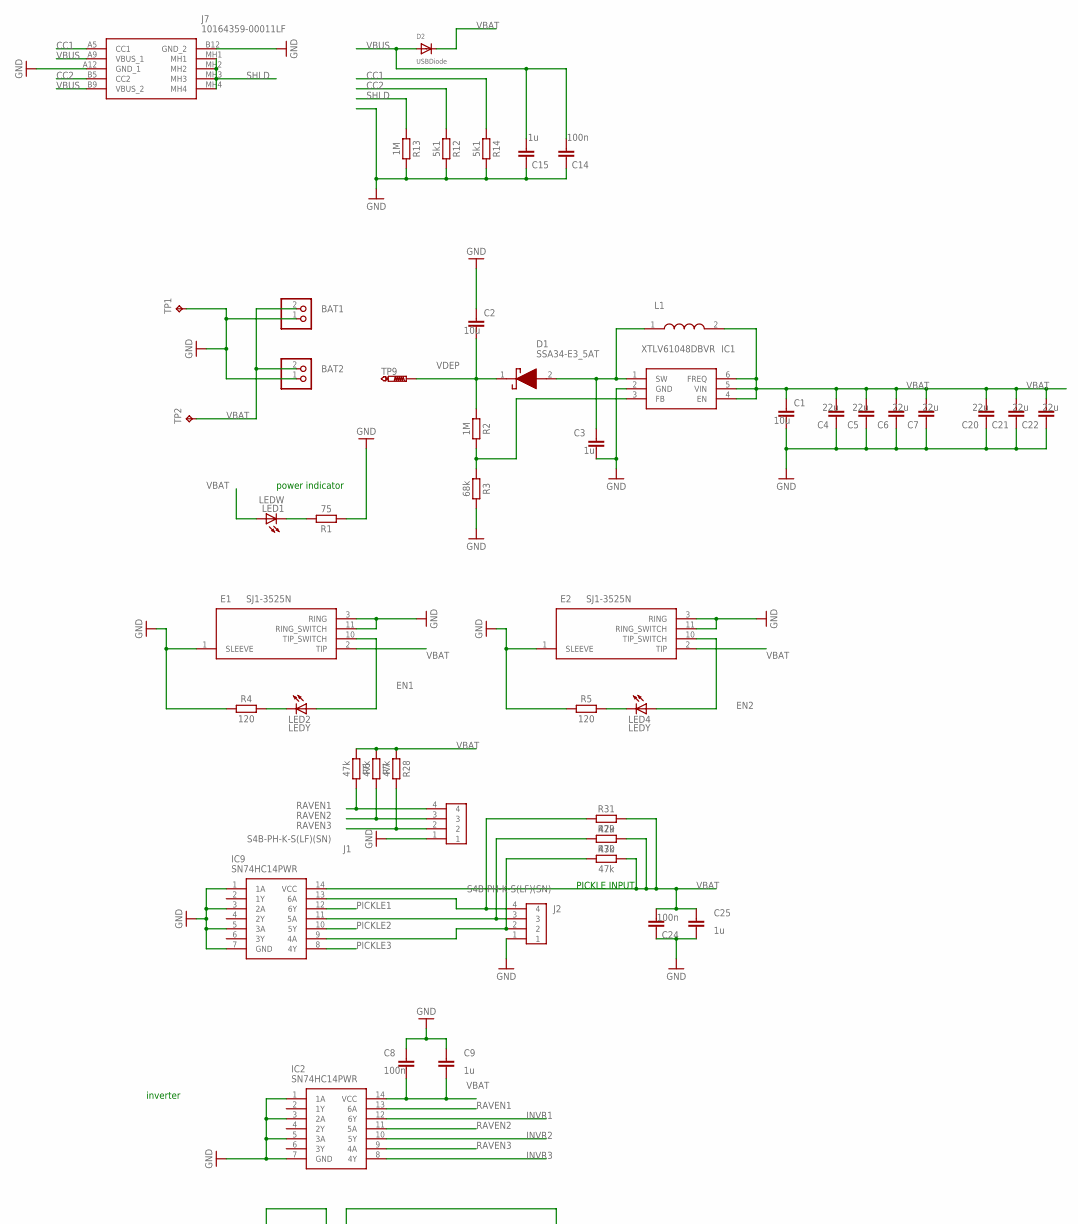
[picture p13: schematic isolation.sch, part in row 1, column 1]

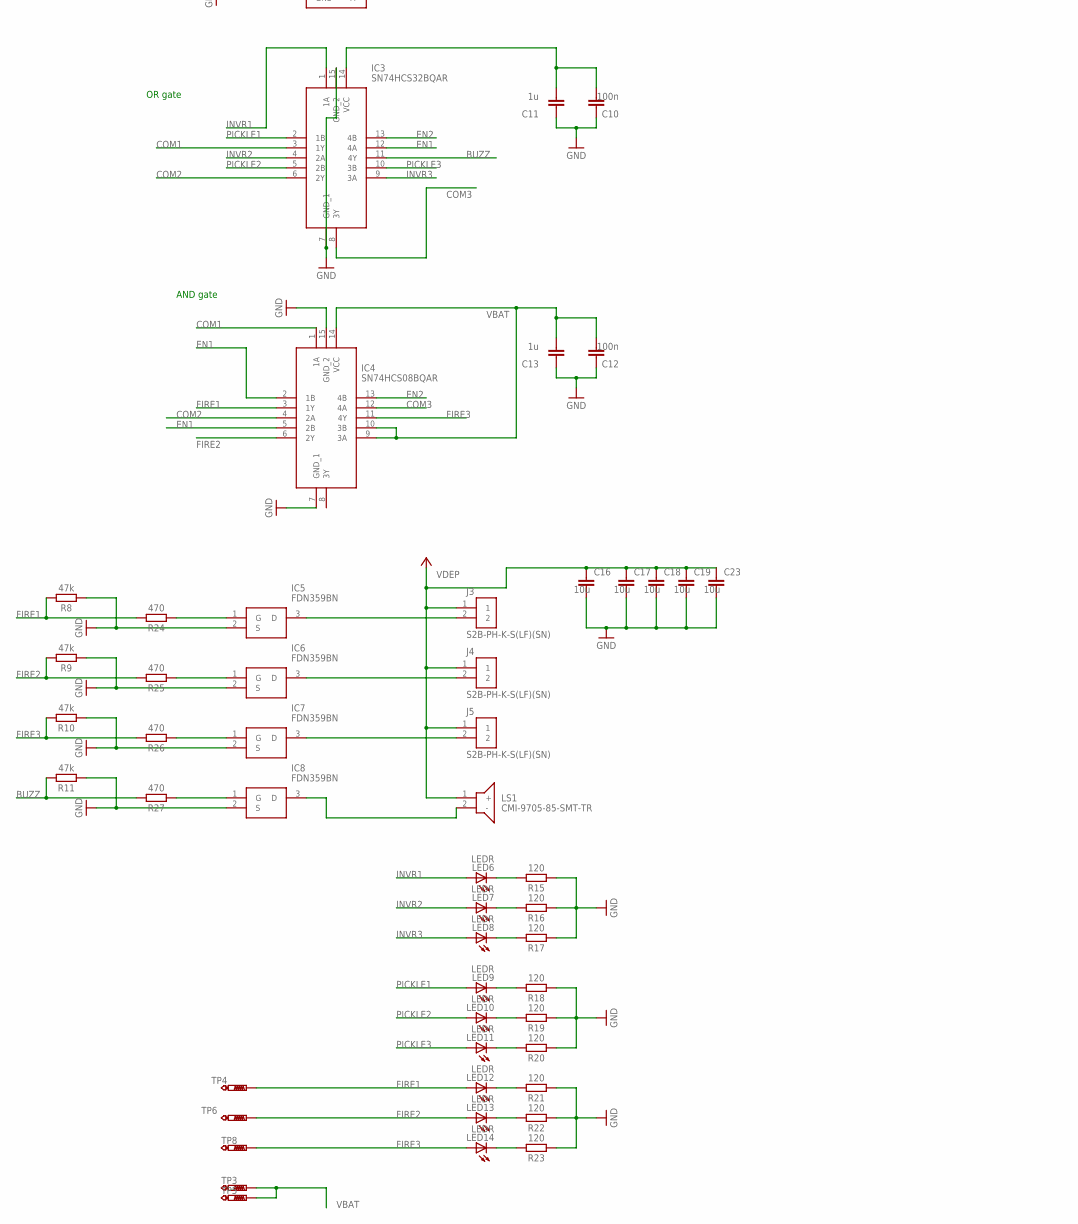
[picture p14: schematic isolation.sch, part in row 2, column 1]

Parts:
BAT1, BAT2: JST_2PIN-THM-RA; JST-PH-2-THM-RA
C1: 10u; CAPC1005X60
C2, C16, C17, C18, C19, C23: 10u; CAPC1608X85
C3, C9, C11, C13, C15, C25: 1u; CAPC1005X60
C4, C5, C6, C7, C20, C21, C22: 22u; CAPC1608X85
C8, C10, C12, C14, C24: 100n; CAPC1005X60
D1: SSA34-E3_5AT; DIOM5127X229N
D2: USBDiode; SOD-123FL
E1, E2: SJ1-3525N; SJ13525N
IC1: XTLV61048DBVR; SOT95P280X145-6N
IC2, IC9: SN74HC14PWR; SOP65P640X120-14N
IC3: SN74HCS32BQAR
IC4: SN74HCS08BQAR
IC5, IC6, IC7, IC8: FDN359BN; SOT95P251X112-3N
J1, J2: S4B-PH-K-S(LF)(SN)
J3, J4, J5: S2B-PH-K-S(LF)(SN)
J7: 10164359-00011LF; 1016435900011LF
L1: 10μH; BMRF00060630100MA1
LED1: LEDW; CHIPLED_0805
LED2, LED4: LEDY; CHIPLED_0805
LED6, LED7, LED8, LED9, LED10, LED11, LED12, LED13, LED14: LEDR; CHIPLED_0805
LS1: CMI-9705-85-SMT-TR; CMI970585SMTTR
R1: 75; RESC1608X60
R2, R13: 1M; RESC1005X40
R3: 68k; RESC1608X60
R4, R5, R15, R16, R17, R18, R19, R20, R21, R22, R23: 120; RESC1005X40
R6, R7, R8, R9, R10, R11, R28, R29, R30, R31: 47k; RESC1005X40
R12, R14: 5k1; RESC1005X40
R24, R25, R26, R27: 470; RESC1005X40
TP1: TPPAD1-13; P1-13
TP2: TPPAD1-17; P1-17
TP3, TP4, TP5, TP6, TP8, TP9: PTR1PAD1-13; P1-13

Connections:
BUZZ: IC3.11 (4Y), R11.2, R27.2
CC1: J7.A5 (CC1), R14.1
CC2: J7.B5 (CC2), R12.1
COM1: IC3.3 (1Y), IC4.1 (1A)
COM2: IC3.6 (2Y), IC4.4 (2A)
COM3: IC3.8 (3Y), IC4.12 (4A)
EN1: E1.10 (TIP_SWITCH), IC3.12 (4A), IC4.2 (1B), IC4.5 (2B), LED2.A
EN2: E2.10 (TIP_SWITCH), IC3.13 (4B), IC4.13 (4B), LED4.A
FIRE1: IC4.3 (1Y), LED12.A, R8.2, R24.2, TP4.TP
FIRE2: IC4.6 (2Y), LED13.A, R9.2, R25.2, TP6.TP
FIRE3: IC4.11 (4Y), LED14.A, R10.2, R26.2, TP8.TP
GND: BAT1.1 (2), BAT2.1 (2), C1.2, C2.1, C3.2, C4.1, C5.1, C6.1, C7.1, C8.1, C9.1, C10.1, C11.1, C12.1, C13.1, C14.1, C15.1, C16.2, C17.2, C18.2, C19.2, C20.1, C21.1, C22.1, C23.2, C24.1, C25.2, E1.1 (SLEEVE), E1.3 (RING), E1.11 (RING_SWITCH), E2.1 (SLEEVE), E2.3 (RING), E2.11 (RING_SWITCH), IC1.2 (GND), IC2.1 (1A), IC2.3 (2A), IC2.5 (3A), IC2.7 (GND), IC3.7 (GND_1), IC3.15 (GND_2), IC4.7 (GND_1), IC4.15 (GND_2), IC5.2 (S), IC6.2 (S), IC7.2 (S), IC8.2 (S), IC9.1 (1A), IC9.3 (2A), IC9.5 (3A), IC9.7 (GND), J1.1, J2.1, J7.A12 (GND_1), J7.B12 (GND_2), R1.1, R3.2, R4.1, R5.1, R8.1, R9.1, R10.1, R11.1, R12.2, R13.2, R14.2, R15.1, R16.1, R17.1, R18.1, R19.1, R20.1, R21.1, R22.1, R23.1, TP1.TP
INVR1: IC2.12 (6Y), IC3.1 (1A), LED6.A
INVR2: IC2.10 (5Y), IC3.4 (2A), LED7.A
INVR3: IC2.8 (4Y), IC3.9 (3A), LED8.A
unnamed: LED1.C, R1.2
unnamed: C3.1, D1.2 (A), IC1.1 (SW), L1.1
unnamed: IC1.3 (FB), R2.2, R3.1
unnamed: LED4.C, R5.2
unnamed: LED2.C, R4.2
unnamed: LED9.C, R18.2
unnamed: LED10.C, R19.2
unnamed: LED11.C, R20.2
unnamed: LED12.C, R21.2
unnamed: LED13.C, R22.2
unnamed: LED14.C, R23.2
unnamed: IC7.3 (D), J5.2
unnamed: IC6.3 (D), J4.2
unnamed: IC9.13 (6A), J2.4, R31.1
unnamed: IC5.3 (D), J3.2
unnamed: LED7.C, R16.2
unnamed: IC9.11 (5A), J2.3, R29.1
unnamed: IC5.1 (G), R24.1
unnamed: IC6.1 (G), R25.1
unnamed: IC8.3 (D), LS1.2 (-)
unnamed: LED8.C, R17.2
unnamed: IC7.1 (G), R26.1
unnamed: IC8.1 (G), R27.1
unnamed: IC9.9 (4A), J2.2, R30.1
unnamed: LED6.C, R15.2
PICKLE1: IC3.2 (1B), IC9.12 (6Y), LED9.A
PICKLE2: IC3.5 (2B), IC9.10 (5Y), LED10.A
PICKLE3: IC3.10 (3B), IC9.8 (4Y), LED11.A
RAVEN1: IC2.13 (6A), J1.4, R6.2
RAVEN2: IC2.11 (5A), J1.3, R7.2
RAVEN3: IC2.9 (4A), J1.2, R28.2
SHLD: J7.MH1, J7.MH2, J7.MH3, J7.MH4, R13.1
VBAT: BAT1.2 (1), BAT2.2 (1), C1.1, C4.2, C5.2, C6.2, C7.2, C8.2, C9.2, C10.2, C11.2, C12.2, C13.2, C20.2, C21.2, C22.2, C24.2, C25.1, D2.C, E1.2 (TIP), E2.2 (TIP), IC1.4 (EN), IC1.5 (VIN), IC1.6 (FREQ), IC2.14 (VCC), IC3.14 (VCC), IC4.9 (3A), IC4.10 (3B), IC4.14 (VCC), IC9.14 (VCC), L1.2, LED1.A, R6.1, R7.1, R28.1, R29.2, R30.2, R31.2, TP2.TP, TP3.TP, TP5.TP
VBUS: C14.2, C15.2, D2.A, J7.A9 (VBUS_1), J7.B9 (VBUS_2)
VDEP: C2.2, C16.1, C17.1, C18.1, C19.1, C23.1, D1.1 (K), J3.1, J4.1, J5.1, LS1.1 (+), R2.1, TP9.TP

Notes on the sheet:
power indicator
inverter
OR gate
AND gate
PICKLE INPUT

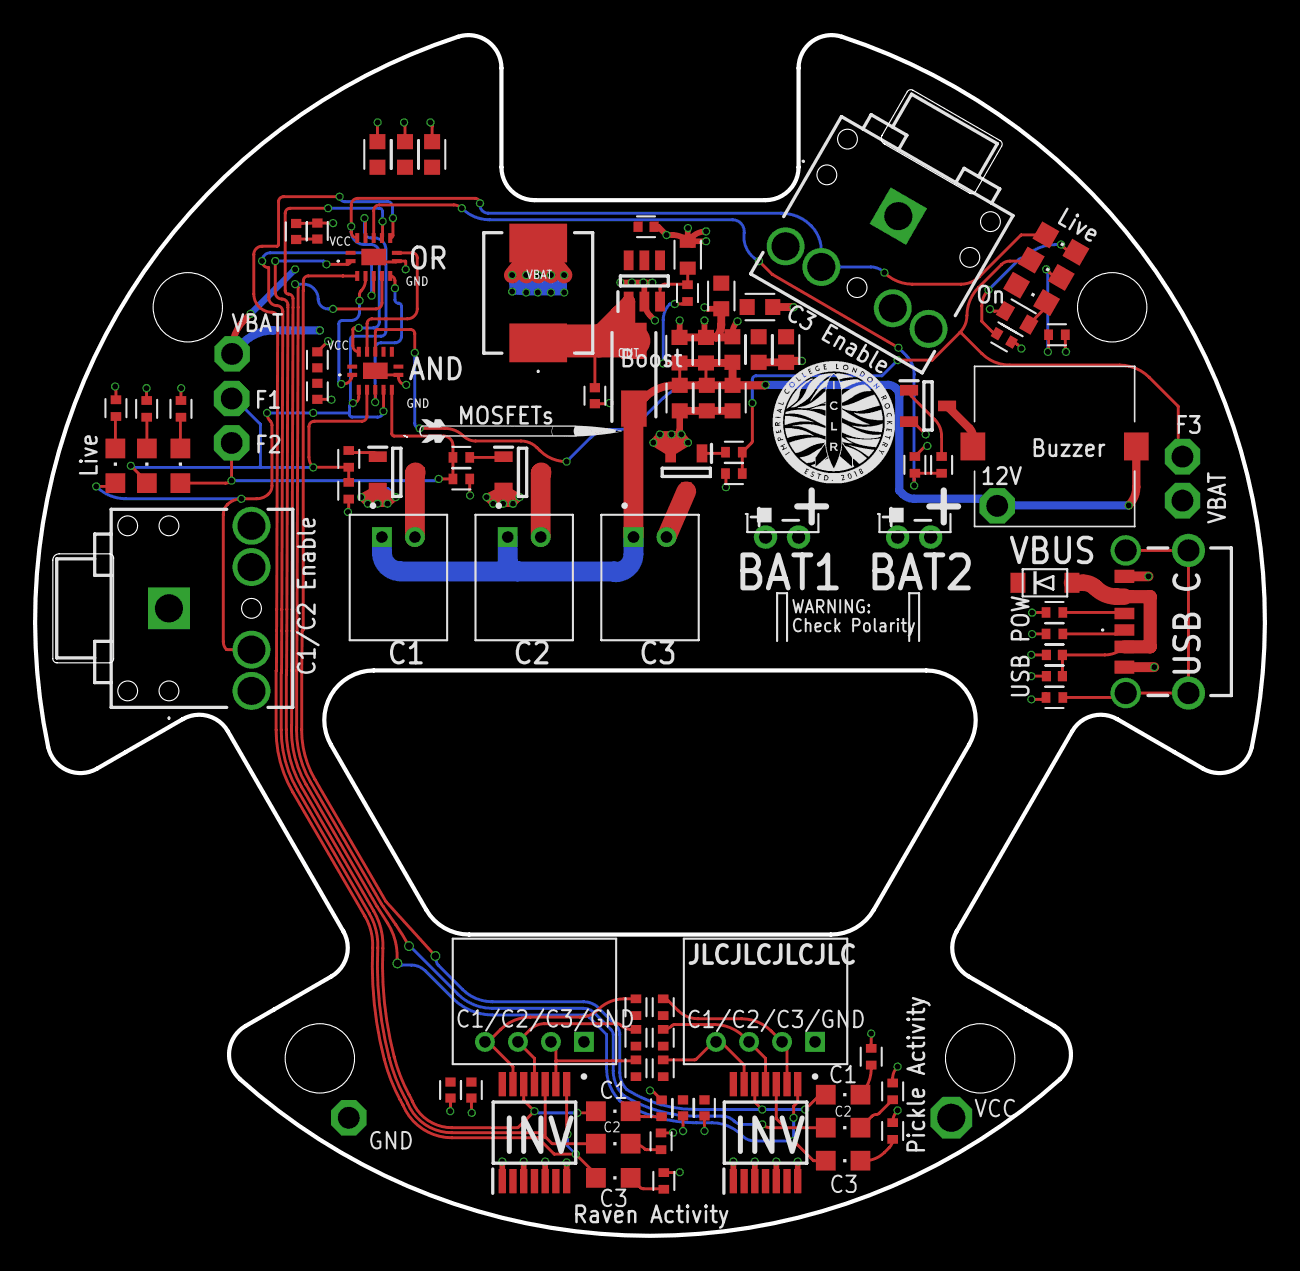
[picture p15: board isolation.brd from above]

Board: 2 copper layers, 74.5 x 72.7 mm, 99 parts (0 on the bottom side), 50 nets.

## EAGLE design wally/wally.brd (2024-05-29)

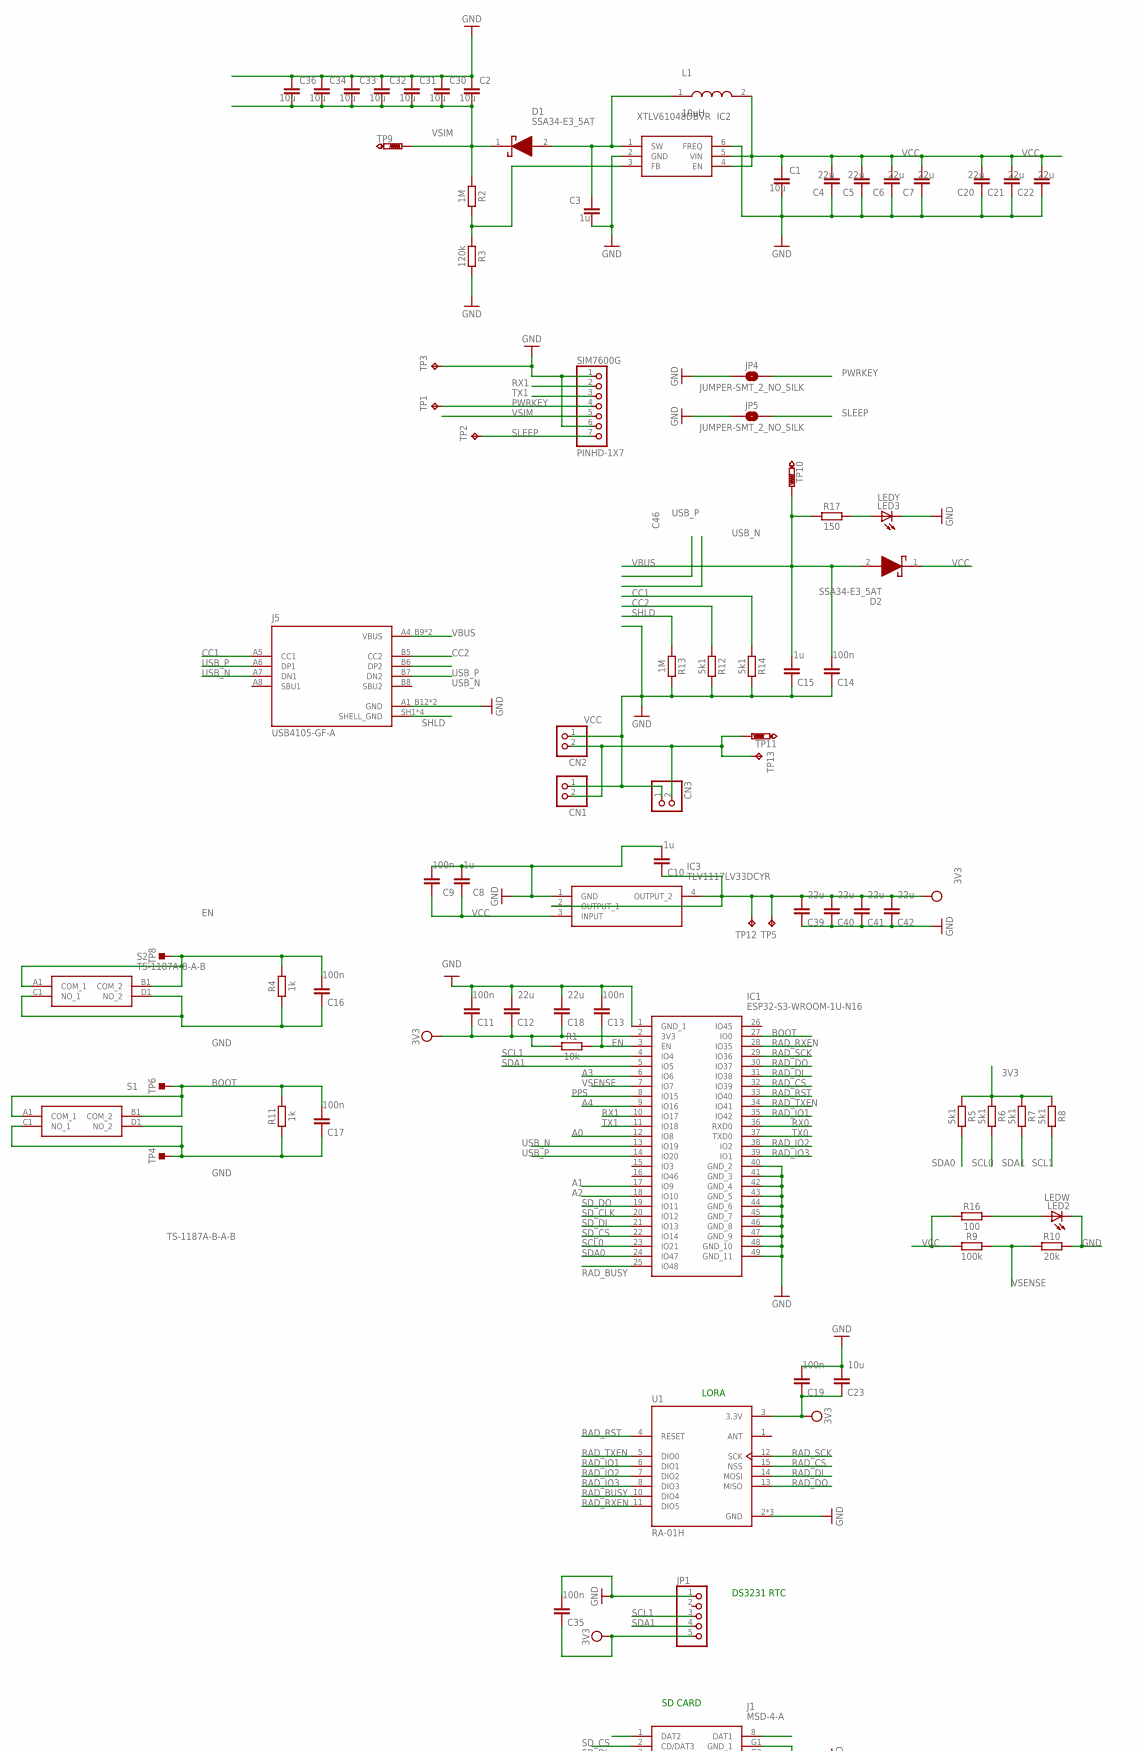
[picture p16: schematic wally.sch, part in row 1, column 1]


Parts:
AC1: H3LIS331DLTR; LIS3DHTR
C1, C23, C24: 10u; CAPC1005X60
C2, C30, C31, C32, C33, C34, C36: 10u; CAPC1608X85
C3, C8, C10, C15, C44, C46: 1u; CAPC1005X60
C4, C5, C6, C7, C12, C18, C20, C21, C22, C39, C40, C41, C42: 22u; CAPC1608X85
C9, C11, C13, C14, C16, C17, C19, C25, C26, C27, C28, C29, C35, C37, C38, C43, C45: 100n; CAPC1005X60
CN1, CN2, CN3: JST_2PIN-THM-RA; JST-PH-2-THM-RA
D1, D2: SSA34-E3_5AT; DIOM5127X229N
IC1: ESP32-S3-WROOM-1U-N16; ESP32S3WROOM1UN16
IC2: XTLV61048DBVR; SOT95P280X145-6N
IC3: TLV1117LV33DCYR; SOT230P700X180-4N
IC4: DPS368XTSA1
IC6: LSM6DSV16BXTR
IC7: MMC5983MA
IC8: APDS-9253-001; APDS9253001
IC9: BME688
J1: MSD-4-A; MSD4A
J2, J3: QWIIC_RIGHT_ANGLE; JST04_1MM_RA
J5: USB4105-GF-A; GCT_USB4105-GF-A
J6: FEMALE 2x3; 2X3-NS
JP1, JP2: PINHD-1X5; 1X05
JP3: PINHD-1X4; 1X04
JP4, JP5: JUMPER-SMT_2_NO_SILK; SMT-JUMPER_2_NO_SILK
L1: 10uH; BMRF00060630100MA1
LED1, LED4: LEDG; CHIPLED_0805
LED2: LEDW; CHIPLED_0805
LED3, LED5: LEDY; CHIPLED_0805
LED6: LEDR; CHIPLED_0805
R1: 10k; RESC1005X40
R2: 1M; RESC1608X60
R3: 120k; RESC1608X60
R4, R11: 1k; RESC1005X40
R5, R6, R7, R8: 5k1; RESC1005X40
R9: 100k; RESC1005X40
R10: 20k; RESC1005X40
R12, R14: 5k1; RESC1608X60
R13: 1M; RESC1005X40
R15, R18: 33; RESC1005X40
R16: 100; RESC1005X40
R17: 150; RESC1608X60
R19: 75; RESC1608X60
R20: 51; RESC1608X60
S1, S2: TS-1187A-B-A-B; TS1187ABAB
SIM7600G: PINHD-1X7; 1X07
TP1, TP2, TP3, TP5, TP12, TP13: TPPAD1-13; P1-13
TP4, TP6, TP8: TESTPOINT_TPS-PAD-036; TESTPOINT_PAD-036
TP9, TP10, TP11: PTR1PAD1-13; P1-13
U1: RA-01H; XCVR_RA-01H

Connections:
3V3: AC1.1 (VDD_IO), AC1.8 (CS), AC1.14 (VDD), AC1.15 (RESERVED_2), C10.1, C11.1, C12.1, C18.1, C19.1, C23.1, C25.1, C26.1, C27.1, C28.1, C29.1, C35.1, C37.1, C38.1, C39.2, C40.2, C41.2, C42.2, C43.1, C44.1, C45.1, C46.1, IC1.2 (3V3), IC3.2 (OUTPUT_1), IC3.4 (OUTPUT_2), IC4.2 (CSB), IC4.5 (SDO), IC4.6 (VDDIO), IC4.8 (VDD), IC6.5 (VDD_IO), IC6.8 (VDD), IC6.12 (CS), IC7.2 (VDD), IC7.4 (SPI_CS), IC7.13 (VDDIO), IC8.4 (VDD), IC9.2 (CSB), IC9.6 (VDDIO), IC9.8 (VDD), J1.4 (VDD), J2.2, J3.2, JP1.5, JP3.1, R1.1, R5.1, R6.1, R7.1, R8.1, TP5.TP, TP12.TP, U1.3 (3.3V)
A0: IC1.12 (IO8), J6.2, LED6.A
A1: IC1.17 (IO9), J6.4, LED5.A
A2: IC1.18 (IO10), J6.6, LED4.A
A3: IC1.6 (IO6), J6.3
A4: IC1.9 (IO16), J6.5
BOOT: C17.2, IC1.27 (IO0), R11.2, S1.A1 (COM_1), S1.B1 (COM_2), TP6.1
CC1: J5.A5 (CC1), R14.1
CC2: J5.B5 (CC2), R12.1
EN: C13.1, C16.2, IC1.3 (EN), R1.2, R4.2, S2.A1 (COM_1), S2.B1 (COM_2), TP8.1
GND: AC1.5 (GND_1), AC1.7 (SDO_SA0), AC1.10 (RESERVED_1), AC1.12 (GND_2), AC1.13 (GND_3), AC1.16 (GND_4), C1.2, C2.1, C3.2, C4.1, C5.1, C6.1, C7.1, C8.2, C9.2, C10.2, C11.2, C12.2, C13.2, C14.1, C15.1, C16.1, C17.1, C18.2, C19.2, C20.1, C21.1, C22.1, C23.2, C24.2, C25.2, C26.2, C27.2, C28.2, C29.2, C30.1, C31.1, C32.1, C33.1, C34.1, C35.2, C36.1, C37.2, C38.2, C39.1, C40.1, C41.1, C42.1, C43.2, C44.2, C45.2, C46.2, CN1.1 (2), CN2.1 (2), CN3.1 (2), IC1.1 (GND_1), IC1.40 (GND_2), IC1.41 (GND_3), IC1.42 (GND_4), IC1.43 (GND_5), IC1.44 (GND_6), IC1.45 (GND_7), IC1.46 (GND_8), IC1.47 (GND_9), IC1.48 (GND_10), IC1.49 (GND_11), IC2.2 (GND), IC2.6 (FREQ), IC3.1 (GND), IC4.1 (GND_1), IC4.7 (GND_2), IC6.1 (SDO/SA0), IC6.2 (TDMOUT), IC6.3 (BCLK), IC6.6 (AH1/QVAR1), IC6.7 (GND), IC7.9 (GND_1), IC7.11 (GND_2), IC8.1 (GND), IC9.1 (GND_1), IC9.5 (SDO), IC9.7 (GND_2), J1.6 (VSS), J1.G1 (GND_1), J1.G2 (GND_2), J1.G3 (GND_3), J1.G4 (GND_4), J2.1, J3.1, J5.A1_B12 (GND), J5.B1_A12 (GND), J6.1, JP1.1, JP2.2, JP3.4, JP4.1, JP5.1, LED2.C, LED3.C, R3.2, R4.1, R10.2, R11.1, R12.2, R13.2, R14.2, R15.2, R18.2, R19.2, R20.2, S1.C1 (NO_1), S1.D1 (NO_2), S2.C1 (NO_1), S2.D1 (NO_2), SIM7600G.1, SIM7600G.6, TP3.TP, TP4.1, U1.2 (GND), U1.9 (GND), U1.16 (GND)
unnamed: LED1.C, R15.1
unnamed: C3.1, D1.2 (A), IC2.1 (SW), L1.1
unnamed: IC2.3 (FB), R2.2, R3.1
unnamed: LED3.A, R17.2
unnamed: C24.1, IC7.10 (CAP)
unnamed: LED4.C, R18.1
unnamed: LED5.C, R19.1
unnamed: LED2.A, R16.2
unnamed: LED6.C, R20.1
unnamed: J1.CD1, LED1.A
PPS: IC1.8 (IO15), JP2.5
PWRKEY: JP4.2, SIM7600G.4, TP1.TP
RAD_BUSY: IC1.25 (IO48), U1.10 (DIO4)
RAD_CS: IC1.32 (IO39), U1.15 (NSS)
RAD_DI: IC1.31 (IO38), U1.14 (MOSI)
RAD_DO: IC1.30 (IO37), U1.13 (MISO)
RAD_IO1: IC1.35 (IO42), U1.6 (DIO1)
RAD_IO2: IC1.38 (IO2), U1.7 (DIO2)
RAD_IO3: IC1.39 (IO1), U1.8 (DIO3)
RAD_RST: IC1.33 (IO40), U1.4 (RESET)
RAD_RXEN: IC1.28 (IO35), U1.11 (DIO5)
RAD_SCK: IC1.29 (IO36), U1.12 (SCK)
RAD_TXEN: IC1.34 (IO41), U1.5 (DIO0)
RX0: IC1.36 (RXD0), JP3.3
RX1: IC1.10 (IO17), JP2.4, SIM7600G.2
SCL0: AC1.4 (SCL_SPC), IC1.23 (IO21), IC4.4 (SCK), IC6.13 (SCL), IC7.1 (SCL/SPI_SCK), IC8.6 (SCL), IC9.4 (SCK), J2.4, R6.2
SCL1: IC1.4 (IO4), J3.4, JP1.3, R8.2
SDA0: AC1.6 (SDA_SDI_SDO), IC1.24 (IO47), IC4.3 (SDI), IC6.14 (SDA), IC7.16 (SDA/SPI_SDI), IC8.5 (SDA), IC9.3 (SDI), J2.3, R5.2
SDA1: IC1.5 (IO5), J3.3, JP1.4, R7.2
SD_CLK: IC1.20 (IO12), J1.5 (CLK)
SD_CS: IC1.22 (IO14), J1.2 (CD/DAT3)
SD_DI: IC1.21 (IO13), J1.3 (CMD)
SD_DO: IC1.19 (IO11), J1.7 (DAT0)
SHLD: J5.SH1 (SHELL_GND), J5.SH2 (SHELL_GND), J5.SH3 (SHELL_GND), J5.SH4 (SHELL_GND), R13.1
SLEEP: JP5.2, SIM7600G.7, TP2.TP
TX0: IC1.37 (TXD0), JP3.2
TX1: IC1.11 (IO18), JP2.3, SIM7600G.3
USB_N: IC1.13 (IO19), J5.A7 (DN1), J5.B7 (DN2)
USB_P: IC1.14 (IO20), J5.A6 (DP1), J5.B6 (DP2)
VBUS: C14.2, C15.2, D2.2 (A), J5.A4_B9 (VBUS), J5.B4_A9 (VBUS), R17.1, TP10.TP
VCC: C1.1, C4.2, C5.2, C6.2, C7.2, C8.1, C9.1, C20.2, C21.2, C22.2, CN1.2 (1), CN2.2 (1), CN3.2 (1), D2.1 (K), IC2.4 (EN), IC2.5 (VIN), IC3.3 (INPUT), JP2.1, L1.2, R9.1, R16.1, TP11.TP, TP13.TP
VSENSE: IC1.7 (IO7), R9.2, R10.1
VSIM: C2.2, C30.2, C31.2, C32.2, C33.2, C34.2, C36.2, D1.1 (K), R2.1, SIM7600G.5, TP9.TP

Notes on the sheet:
DS3231 RTC
LORA
SD CARD
BARO
IMU
HR_ACC
MAG


Board: 2 copper layers, 41.0 x 101.0 mm, 113 parts (0 on the bottom side), 54 nets.

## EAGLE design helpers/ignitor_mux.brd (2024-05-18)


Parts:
J1, J2, J3, J4: S2B-PH-K-S(LF)(SN)

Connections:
FIRE: J1.1, J2.1, J3.1, J4.1
GND: J1.2, J2.2, J3.2, J4.2

Board: 2 copper layers, 4 parts (0 on the bottom side), 2 nets, no tracks yet.

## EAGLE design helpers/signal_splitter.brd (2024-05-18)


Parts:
J1, J2, J3: S4B-PH-K-S(LF)(SN)

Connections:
C1: J1.4, J2.4, J3.4
C2: J1.3, J2.3, J3.3
C3: J1.2, J2.2, J3.2
GND: J1.1, J2.1, J3.1


Board: 2 copper layers, 22.9 x 25.4 mm, 3 parts (0 on the bottom side), 4 nets.

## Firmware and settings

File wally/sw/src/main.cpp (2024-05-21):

#include <Arduino.h>

// put function declarations here:
int myFunction(int, int);

void setup() {
  // put your setup code here, to run once:
  float supplyVoltage = getTrueVoltage();
  if (supplyVoltage < 3.84) {
    digitalWrite(LED_R, HIGH);
    digitalWrite(LED_Y, LOW);
    digitalWrite(LED_G, LOW);
  }
  else if (supplyVoltage < 4.02) {
    digitalWrite(LED_R, HIGH);
    digitalWrite(LED_Y, HIGH);
    digitalWrite(LED_G, LOW);
  }
  else {
    digitalWrite(LED_R, HIGH);
    digitalWrite(LED_Y, HIGH);
    digitalWrite(LED_G, HIGH);
  }
}

void loop() {
  // put your main code here, to run repeatedly:
}

// put function definitions here:
int myFunction(int x, int y) {
  return x + y;
}

float getVoltageRaw() {
  return analogReadMilliVolts(VSENSE);
}

float getTrueVoltage() {
  float raw = getVoltageRaw();
  return (raw * (100 + 20))/20; // voltage divider
}

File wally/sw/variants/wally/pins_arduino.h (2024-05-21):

#ifndef Pins_Arduino_h
#define Pins_Arduino_h

#include <stdint.h>
#include "soc/soc_caps.h"

#define USB_VID            0x239A
#define USB_PID            0x8145
#define USB_MANUFACTURER   "ICLR"
#define USB_PRODUCT        "WALLY"
#define USB_SERIAL         ""   // Empty string for MAC adddress

#define PIN_BUTTON1     0  // BOOT0 switch

// UART
static const uint8_t TX0 = 43;
static const uint8_t RX0 = 44;

static const uint8_t TX1 = 17;
static const uint8_t RX1 = 18;

// I2C
static const uint8_t SDA0 = 47;
static const uint8_t SCL0 = 21;

static const uint8_t SDA1 = 5;
static const uint8_t SCL1 = 4;

// SD
static const uint8_t SD_CS   = 14;
static const uint8_t SD_DO   = 42;
static const uint8_t SD_CLK  = 39;
static const uint8_t SD_DI   = 21;

// Radio
static const uint8_t RAD_CS   = 39;
static const uint8_t RAD_DO   = 37;
static const uint8_t RAD_CLK  = 36;
static const uint8_t RAD_DI   = 38;

// GPIO
static const uint8_t A0 = 8;
static const uint8_t A1 = 10;
static const uint8_t A2 = 9;
static const uint8_t A3 = 6;
static const uint8_t A4 = 16;

#define LED_R    8
#define LED_Y   10
#define LED_G    9

// VSENSE
static const uint8_t VSENSE = 7;

// PPS
static const uint8_t PPS = 15;

#endif /* Pins_Arduino_h */

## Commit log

2023-02-07 wally board with gps and lora
    [WallyTest.sch]
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2024-04-25 create blank schematics for isolation board
    [isolation.brd, isolation.sch]
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2024-04-26 12v boost schematic complete
    [isolation.brd, isolation.sch]
2024-04-26 headphone jacks for user input
    [isolation.brd, isolation.sch]
2024-04-26 fix footprint for caps
    [isolation.brd, isolation.sch]
2024-04-26 headphone jack with inverter
    [isolation.brd, isolation.sch]
2024-04-26 jst inputs from flight computers
    [isolation.brd, isolation.sch]
2024-04-26 invert raven inputs
    [isolation.brd, isolation.sch]
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2024-04-26 pull down resistors on mosfets
    [isolation.brd, isolation.sch]
2024-04-26 danger buzzer
    [isolation.brd, isolation.sch]
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2024-04-26 indicator LEDs with manual testing
    [isolation.brd, isolation.sch]
2024-04-26 ust jst for power
    [isolation.brd, isolation.sch]
2024-04-26 layout with stringers and xc
    [isolation.brd, isolation.sch]
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2024-04-27 set board outline from dxf
    [isolation.brd]
2024-04-27 pads for ext power in
    [isolation.brd, isolation.sch]
2024-04-27 ground and vcc pours
    [isolation.brd]
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2024-04-27 move to smaller inverter
    [isolation.brd, isolation.sch]
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2024-04-27 2 pin ignitor connectors
    [isolation.brd, isolation.sch]
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2024-04-27 fix to drc
    [isolation.brd]
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2024-04-27 import cutout from fusion
    [cutout.dxf, isolation.brd]
2024-04-27 add some bulk caps
    [isolation.brd, isolation.sch]
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2024-04-27 fix assembly
    [isolation.brd, isolation.sch, isolation_top_bom.csv]
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2024-04-27 more clearance around vias
    [bom.xlsx, isolation.brd]
2024-04-27 make a mux board for ignitors
    [ignitor_mux.brd, ignitor_mux.sch]
2024-04-28 generate gerber for mux
    [ignitor_mux.brd]
2024-04-28 create a jst splitter pcb
    [jst_splitter.brd, jst_splitter.sch]
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2024-04-28 fix drc issues
    [isolation.brd]
2024-04-28 initialise wally design
    based on ESP32-S3 and AI Thinker RA01-H
    [wally.brd, wally.sch]
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2024-04-28 SIM7600G (treat as pin header)
    [wally.brd, wally.sch]
2024-04-28 Boost circuit for SIM
    [wally.brd, wally.sch]
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2024-04-28 add ds3231 rtc
    treat as 5 pin header
    [wally.brd, wally.sch]
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2024-04-28 switch to smaller esp
    [wally.brd, wally.sch]
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2024-04-29 complete placement of flight board components
    [wally.brd, wally.sch]
2024-04-29 add ground station gps support
    [wally.brd, wally.sch]
2024-04-29 manual route important traces
    before letting autorouter do it for me lol
    [wally.brd, wally.sch]
2024-04-29 more test points for mystery pins
    [wally.brd, wally.sch]
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2024-04-29 autoroute with thicker traces
    [wally.brd]
2024-04-29 add some status LEDs
    [wally.brd, wally.sch]
2024-04-29 fix all airwires
    [wally.brd, wally.sch]
2024-04-29 fix to jlc drc
    [wally.brd]
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2024-04-29 cutout so board can be safely beheaded
    [wally.brd]
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2024-04-30 wally ready for manufacture
    [bom.xlsx, wally_bom.xlsx, wally_top_bom.csv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]
2024-04-30 create signal splitter board
    4 pin jst ph (2mm), compatible with isolation board
    [signal_splitter.brd, signal_splitter.sch]
2024-04-30 move helper boards to their own section
    [ignitor_mux.brd, ignitor_mux.sch, jst_splitter.brd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]
2024-04-30 swap usb c connector
    [isolation.brd, isolation.sch]
2024-04-30 swap usb c
    [bom.xlsx, wally.brd, wally.sch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]
2024-04-30 swap usb c (again)
    now using USB4105-GF-A-120, consistent with WALLY
    [isolation.brd, isolation.sch]
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2024-05-02 increase keepout area near break line
    [wally.brd]
2024-05-14 remove parallel vbus diodes
    [isolation.brd, isolation.sch]
2024-05-14 move all components to top
    [isolation.brd]
2024-05-14 flip all components to top
    [isolation.brd]
2024-05-14 reset layout
    [isolation.brd]
2024-05-14 reset routing
    [isolation.brd]
2024-05-15 increase pour spacing to allow filing
    [isolation.brd, isolation.sch]
2024-05-15 add mill slot for headphone jack
    [isolation.brd]
2024-05-15 move traces away from edge
    [isolation.brd]
2024-05-15 add mosfet gate drive resistors
    [isolation.brd, isolation.sch]
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2024-05-15 import outline from fusion, add mounts
    [pdu.brd]
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2024-05-15 initial mosfet with RC
    [pdu.brd, pdu.sch]
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2024-05-15 fix hole position
    [pdu.brd]
2024-05-15 add usb c (optional)
    [pdu.brd, pdu.sch]
2024-05-15 add output with decoupling cap
    [pdu.brd, pdu.sch]
2024-05-15 fill length with conns
    [pdu.brd, pdu.sch]
2024-05-15 swap connector
    [pdu.brd, pdu.sch]
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2024-05-16 fix lte orientation
    [wally.brd, wally.sch]
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2024-05-16 fix gps pin order
    [wally.brd, wally.sch]
2024-05-16 fix bat polarity
    [wally.brd, wally.sch]
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2024-05-17 move connectors around for better mech integration
    [pdu.brd]
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2024-05-17 switch to power only usb
    [isolation.brd, isolation.sch]
2024-05-17 cutout for 3.5mm connector
    [isolation.brd, isolation.sch]
2024-05-17 helper boards prod files
    [ignitor_mux.brd, jst_splitter.brd, jst_splitter.sch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]
2024-05-17 add test fire points
    [isolation.brd, isolation.sch]
2024-05-18 souvenir edition of pdu
    [pdu_souvenir.brd, pdu_souvenir.sch, wally.brd]
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2024-05-18 remove adafruit warning
    they didn't make this :)
    [variant.cpp]
2024-05-18 add two generic inputs to wally
    had two gpio left lol
    [bom.xlsx, wally.brd, wally.sch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]
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2024-05-19 move rtc to separate i2c bus
    allows all sensors to run at high speed
    [wally.sch]
2024-05-19 remove thermocouple amp
    makes more sense to have it externally and connected through i2c
    [wally.brd, wally.sch]
2024-05-19 use smaller components where available
    [wally.brd, wally.sch]
2024-05-19 change to lsm6dsv imu
    +- 32g and integrated sensor fusion
    [wally.brd, wally.sch]
2024-05-20 add high range accel
    [wally.sch]
2024-05-20 add extended range baro
    [wally.sch]
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2024-05-20 swap mag IC
    [wally.sch]
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2024-05-20 swap hr baro with bme
    [wally.sch]
2024-05-20 swap to dps368
    dps310 is nrnd
    [wally.sch]
2024-05-20 change i2c pullup vals
    move to 5k1 from 10k
    [wally.sch]
2024-05-20 route new i2c traces
    [wally.brd, wally.sch]
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2024-05-21 add mounting hole, ground plane under usb data
    [wally.brd, wally.sch]
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2024-05-26 invert pickle signals
    [isolation.sch]
2024-05-26 remove safe indicator led
    much easier to wire
    [isolation.sch]
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2024-05-26 fix silkscreen after moving components
    [isolation.brd, isolation.sch]
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2024-05-28 improve routing
    swap gnd and supply planes and then reroute everything
    [isolation.brd, isolation.sch]
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2024-05-29 aluminium single layer version
    souvenir only lol (but still technically functional!)
    [pdu_sval.brd, pdu_sval.sch]
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

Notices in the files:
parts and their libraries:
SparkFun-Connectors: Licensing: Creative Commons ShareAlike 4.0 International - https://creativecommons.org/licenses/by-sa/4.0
